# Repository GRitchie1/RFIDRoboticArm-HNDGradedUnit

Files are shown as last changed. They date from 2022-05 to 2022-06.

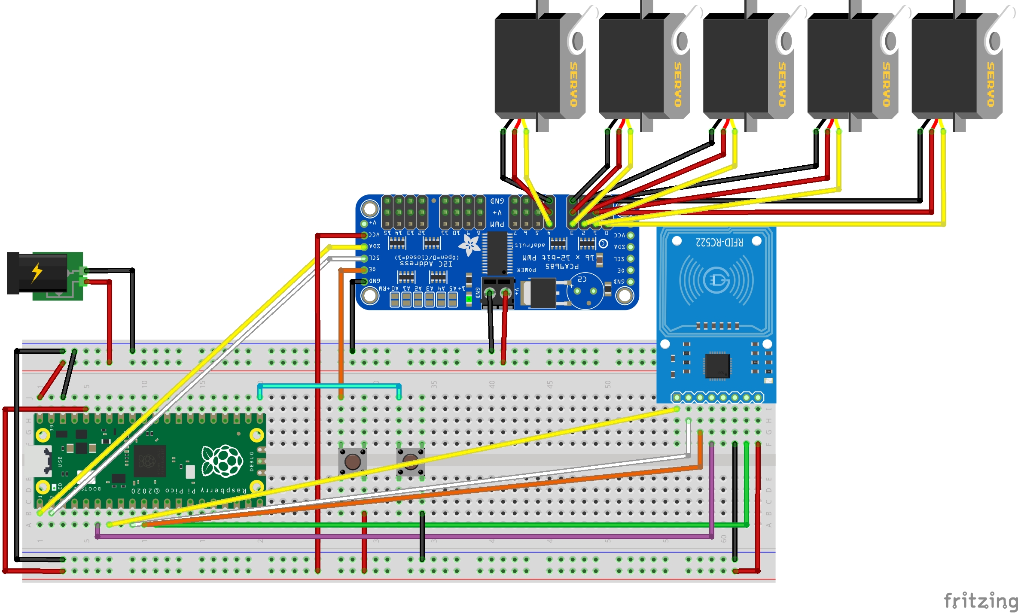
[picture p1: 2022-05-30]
Wiring Diagrams/Full Wiring Diagram_bb.jpg

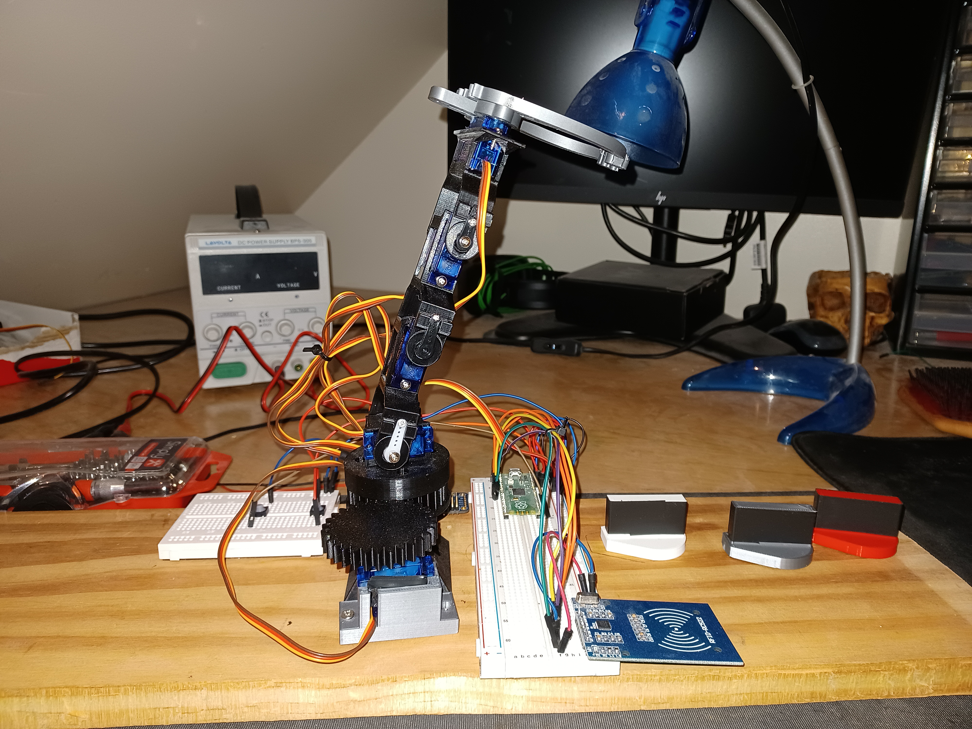
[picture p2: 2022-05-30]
Images/ (1).jpg

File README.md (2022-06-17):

# Graded-Unit RFID Robotic Arm Project

This project was completed as part of my HND Mechatronics Graded Unit.  This project was awarded an 'A' Grade.  The client required a robotic arm to pick up, identify and sort items based on RFID codes.

Images of the completed system can be found [here](https://github.com/GRitchie1/RFIDRoboticArm-HNDGradedUnit/tree/main/Images).

All of the models used can be found [here](https://github.com/GRitchie1/Graded-Unit/tree/main/Models), and are 3D printable.

The code was written as part of the project and utilises CircuitPython due to the vast number of libraries.

This repository will be updated with parts lists and instructions.

## Parts List
This project requires access to a 3D printer to manufacture the robot arm.  All of the [models](https://github.com/GRitchie1/Graded-Unit/tree/main/Models) can be 3D printed using PLA.

The required quantities of 3D printed parts are shown in the table below.

| Model | QTY |
|---|-----|
| Base Mount | 1 |
| Driver Gear | 1 |
| Geared Base Bottom | 1 |
| Geared Base Top | 1 |
| Item to Pickup | 3 |
| Linkage 1 & 2 | 2 |
| Linkage 3 | 1 |
| Motor Mount | 1 |

The required quantities of components and other parts are shown below.

| Part | QTY |
|---|-----|
| Pi Pico | 1 |
| Micro Servo (SG92R) | 5 |
| Momentary Push button | 2 |
| RFID Scanner (RC522) | 1 |
| Power supply (5V 3A) | 1 |
| Breadboard friendly power jack | 1 |
| Servo driver (PCA9685) | 1 |
| Skateboard bearing | 2 |
| M8 Bolt | 1 |
| M3 * 12 Countersunk screws | 9 |

## Wiring Diagrams
The wiring diagrams for this project were designed using Fritsing.

Full Wiring Diagram_bb

## Assembly
To assemble the robotic arm, first ensure that you have got all of the required [parts](#Parts-List).

Next use the following steps to assemble the arm:
1. Insert the bearing into the Base (Top) piece. 
2. Insert the bearing into the Base (Bottom) piece.
3. Place the Top and Bottom pieces of the base together and insert the screws to keep them attached.
4. Insert the M8 bolt into the Mount piece.
5. Attach the mount piece to a piece of support material (such as a plank of wood)
6. Assemble the rest of the robot arm using servo motors and linkage pieces.
7. Place the Robot arm onto the M8 bolt.
8. Attach the driver gear to the servo motor.
9. Mount the servo motor to the support material using the motor mount piece at a suitable distance to allow the gears to interlink.

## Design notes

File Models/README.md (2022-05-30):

# Models

## Custom designed models
All of the models were custom designed for this project unless listed below in [Other models](#other-models).

All of the custom models were designed in [FreeCAD](https://www.freecadweb.org/).

All of the models are 3D printable using PLA.

## Other Models

### Linkages
The following models were sourced from Thingiverse and created by [bentommye](https://www.thingiverse.com/bentommye/designs):
- Linkage 1 & 2 (Named Arm_v4_-_mm.stl)
- Linkage 3 (Named ArmFront_v3_-_mm.stl)

They can be found [Here](https://www.thingiverse.com/thing:34829/files).

They are distributed under the [Creative Commons - Attribution License](https://creativecommons.org/licenses/by/4.0/).

### Gripper
The following models were sourced from Thingiverse and created by [Nasir13](https://www.thingiverse.com/nasir13/designs):
- [Gripper](https://www.thingiverse.com/thing:4300387)

They are distributed under the [Creative Commons - Attribution - Share Alike License](https://creativecommons.org/licenses/by-sa/3.0/).

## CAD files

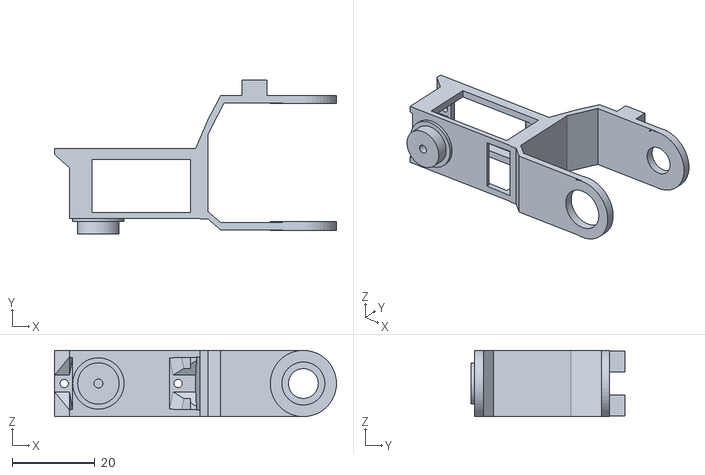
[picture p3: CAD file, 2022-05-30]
Models/Linkage 1 & 2.stl
68.1 x 37.2 x 16.0

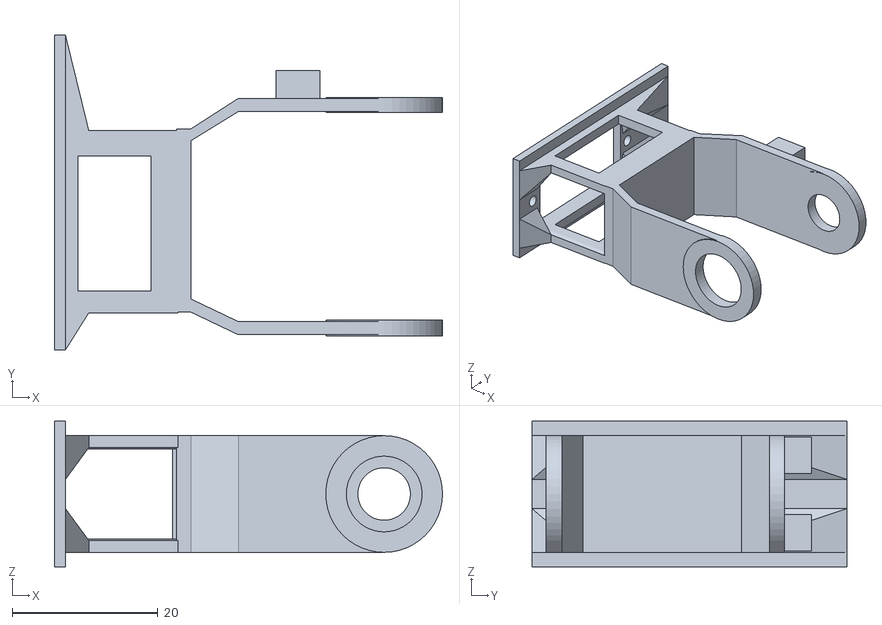
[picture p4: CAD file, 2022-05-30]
Models/Linkage 3.stl
53.2 x 43.2 x 20.0

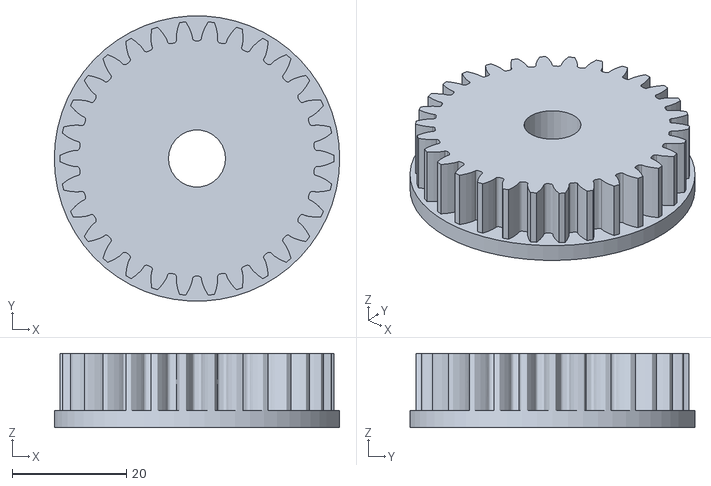
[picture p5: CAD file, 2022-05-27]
Models/Geared Base Bottom.stl
50.0 x 49.9 x 13.0

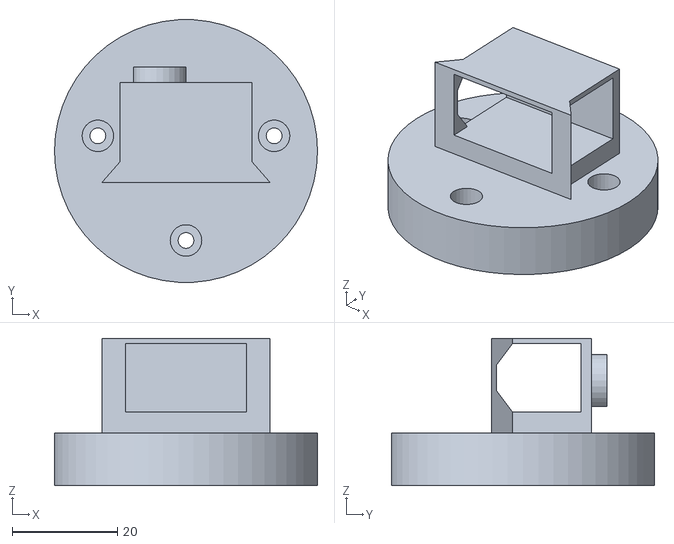
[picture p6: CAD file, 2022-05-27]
Models/Geared Base Top.stl
50.0 x 49.9 x 28.0

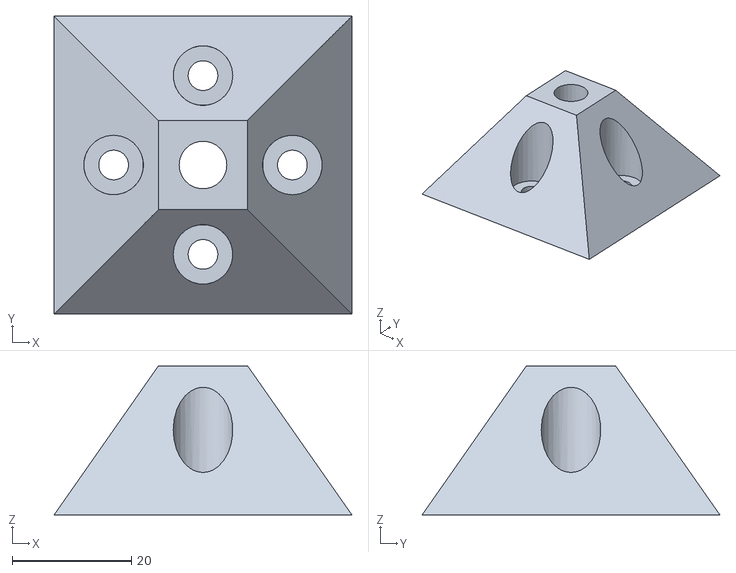
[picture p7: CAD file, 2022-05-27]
Models/Base Mount.stl
50.0 x 50.0 x 25.0

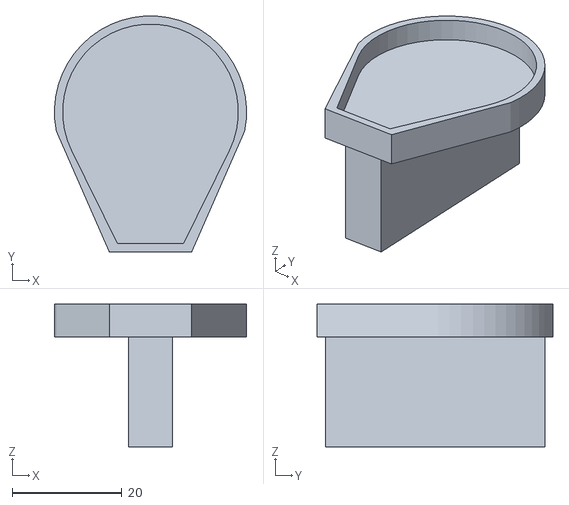
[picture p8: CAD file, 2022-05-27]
Models/Item to Pickup.stl
35.0 x 43.0 x 26.0

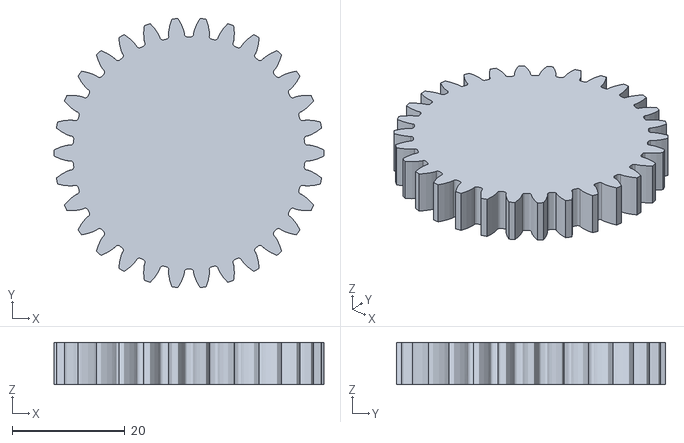
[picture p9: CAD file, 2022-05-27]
Models/Driver Gear.stl
48.0 x 47.8 x 7.50

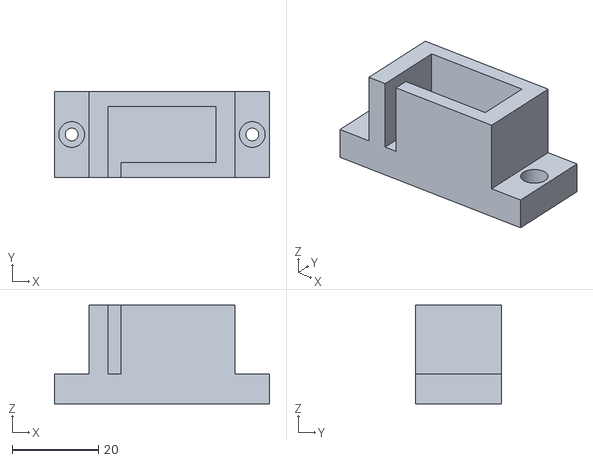
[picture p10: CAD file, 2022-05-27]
Models/Motor Mount.stl
50.0 x 20.0 x 23.0

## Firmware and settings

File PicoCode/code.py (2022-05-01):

import time
import board
import busio
import digitalio
import mfrc522
from adafruit_motor import servo
from adafruit_pca9685 import PCA9685

#Init GPIO
startButton = digitalio.DigitalInOut(board.GP16)
startButton.switch_to_input(pull=digitalio.Pull.UP)

#Init SPI for RFID
sck = board.GP6
mosi = board.GP7
miso = board.GP4
spi = busio.SPI(sck, MOSI=mosi, MISO=miso)

#Init I2C for motor control
i2c = busio.I2C(board.GP1, board.GP0)

#Init RFID
cs = digitalio.DigitalInOut(board.GP5)
rst = digitalio.DigitalInOut(board.GP8)
rfid = mfrc522.MFRC522(spi, cs, rst)
rfid.set_antenna_gain(0x07 << 4)

# Create Servos
pca = PCA9685(i2c)
pca.frequency = 50

base = servo.Servo(pca.channels[0], min_pulse=500, max_pulse=2400)
first = servo.Servo(pca.channels[1], min_pulse=500, max_pulse=2400)
second = servo.Servo(pca.channels[2], min_pulse=500, max_pulse=2400)
third = servo.Servo(pca.channels[3], min_pulse=500, max_pulse=2400)
gripper = servo.Servo(pca.channels[4], min_pulse=500, max_pulse=2400)


#Setup
prev_data = None
prev_time = 0
timeout = 1

#Starting position
base.angle = 1
first.angle = 140
second.angle = 90
third.angle = 50
gripper.angle = 180
time.sleep(2)

def Movement_Cycle():
    #Open Gripper
    print("open gripper")
    for i in range(gripper.angle, 120, -1):
        gripper.angle = i
        time.sleep(0.02)

    #Move to pick up item
    print("Move to pick up item")
    for i in range(first.angle, 80, -1):
        first.angle = i
        time.sleep(0.02)

    for i in range(second.angle, 70, -1):
        second.angle = i
        time.sleep(0.02)

    for i in range(third.angle, 30, -1):
        third.angle = i
        time.sleep(0.02)

    #Close Gripper
    print("Close Gripper")
    for i in range(gripper.angle, 180, 1):
        gripper.angle = i
        time.sleep(0.02)

    #Lift item
    print("Lift item")
    for i in range(first.angle, 140, 1):
        first.angle = i
        time.sleep(0.02)

    for i in range(second.angle, 90, 1):
        second.angle = i
        time.sleep(0.02)

    for i in range(third.angle, 50, 1):
        third.angle = i
        time.sleep(0.02)

    #Rotate to RFID
    print("Rotate to RFID")
    for i in range(base.angle, 40, 1):
        base.angle = i
        time.sleep(0.02)

    #Move to scan item
    print("Move to scan item")
    for i in range(first.angle, 85, -1):
        first.angle = i
        time.sleep(0.02)

    for i in range(second.angle, 60, -1):
        second.angle = i
        time.sleep(0.02)

    #Scan Item
    partID = None
    timer = 0
    while timer < 3 and partID == None:
        data = ReadRFID()
        if data:
            partID = data
            print(data)
        timer+= 1
        time.sleep(1)

    if partID:
        print(f"{partID=}")
    else:
        print("No part detected")


    #Lift after scanning item
    print("Lift after scanning item")
    for i in range(first.angle, 140, 1):
        first.angle = i
        time.sleep(0.02)

    for i in range(second.angle, 90, 1):
        second.angle = i
        time.sleep(0.02)

    #Rotate to Output position

    if partID == "d990e0b8":
        target_output = 90
    elif partID == "f3515416":
        target_output = 145
    else:
        target_output = 180


    print(f"Rotate to Output position {target_output}")
    for i in range(base.angle, target_output, 1):      #Add if statement from scanned ID
        base.angle = i
        time.sleep(0.02)

    #Move to place item
    print("Move to place item")
    for i in range(first.angle, 80, -1):
        first.angle = i
        time.sleep(0.02)

    for i in range(second.angle, 70, -1):
        second.angle = i
        time.sleep(0.02)

    for i in range(third.angle, 30, -1):
        third.angle = i
        time.sleep(0.02)

    #Open Gripper
    print("Open Gripper")
    for i in range(gripper.angle, 120, -1):
        gripper.angle = i
        time.sleep(0.02)

    #Lift arm
    print("Lift arm")
    for i in range(first.angle, 140, 1):
        first.angle = i
        time.sleep(0.02)

    for i in range(second.angle, 90, 1):
        second.angle = i
        time.sleep(0.02)

    for i in range(third.angle, 50, 1):
        third.angle = i
        time.sleep(0.02)

    #Close Gripper
    print("Close Gripper")
    for i in range(gripper.angle, 180, 1):
        gripper.angle = i
        time.sleep(0.02)

    #Rotate to Starting position
    print("Rotate to Starting position")
    for i in range(base.angle, 1, -1):      #Add if statement from scanned ID
        base.angle = i
        time.sleep(0.02)


def ReadRFID():
    global prev_time
    global prev_data

    (status, tag_type) = rfid.request(rfid.REQALL)
    if status == rfid.OK:
        (status, raw_uid) = rfid.anticoll()

        if status == rfid.OK:
            rfid_data = "{:02x}{:02x}{:02x}{:02x}".format(raw_uid[0], raw_uid[1], raw_uid[2], raw_uid[3])

            if rfid_data != prev_data:
                prev_data = rfid_data

                print("Card detected! UID: {}".format(rfid_data))
            prev_time = time.monotonic()
    else:
        if time.monotonic() - prev_time > timeout:
            prev_data = None

    return prev_data


while True:
    if not startButton.value:
        print("Move")
        Movement_Cycle()
    time.sleep(0.1)

pca.deinit()

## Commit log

2021-10-29 Add Servo Class
    Add Servo Class to main to allow addition of more Servo functions
2021-10-29 Add third servo to move
2021-10-31 Add move_smoothly
    Add move smoothly function to servo. This is currently blocking code so must be updated to use non blocking code
2021-10-31 Move Servo Class to Servo.py
    move the servo class and the MIN MAX defaults to the servo.py file
2021-10-31 Add PID movement
    Add PID movement option to Servo Class
2021-10-31 Add RFID to move arm
2021-11-06 Add proportional control to servo class
2022-04-24 attempt simple pwm
2022-04-24 new servo attempt
2022-04-24 Initial code with servo driver board
2022-04-24 Fix base motor
2022-04-24 Add start button
2022-04-24 Copy full pico code into repo
2022-05-27 Update Graded unit project
    [Base Mount.stl, Driver Gear.stl, Geared Base Bottom.stl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]
2022-05-30 Fix wiring diagram
    [Full Wiring Diagram.fzz]
2022-05-30 Add gripper and linkages models
    [Linkage 1 & 2.stl, Linkage 3.stl]
